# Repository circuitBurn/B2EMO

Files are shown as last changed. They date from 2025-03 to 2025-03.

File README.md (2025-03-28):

# B2EMO

### Build Log

#### March 26, 2025
This is still under development!

The PCB is undergoing a revision and will be released once it is built and tested.

I am adding a temporary wiring diagram and for anyone wanting to implement the automated inner ring control.

## Bill of Materials
[BOM](https://github.com/circuitBurn/B2EMO/blob/development/BOM.pdf)

## RF System
* [FrSky Archer Plus R12+](https://www.frsky-rc.com/product/archer-plus-r12/)
* [Horus X10S Express](https://www.frsky-rc.com/product/horus-x10s-express/)

## Arduino Libraries
* [Countdown](https://github.com/RobTillaart/CountDown)
* [DFPlayerMini_Fast](https://github.com/PowerBroker2/DFPlayerMini_Fast)
* [Bolderflight SBUS](https://github.com/bolderflight/sbus)

## Circuit Diagram
This is a temporary circuit diagram outlining the minimum circuit needed to get the ESP32 controlling the ring motors. This will be updated once the PCB is completed.

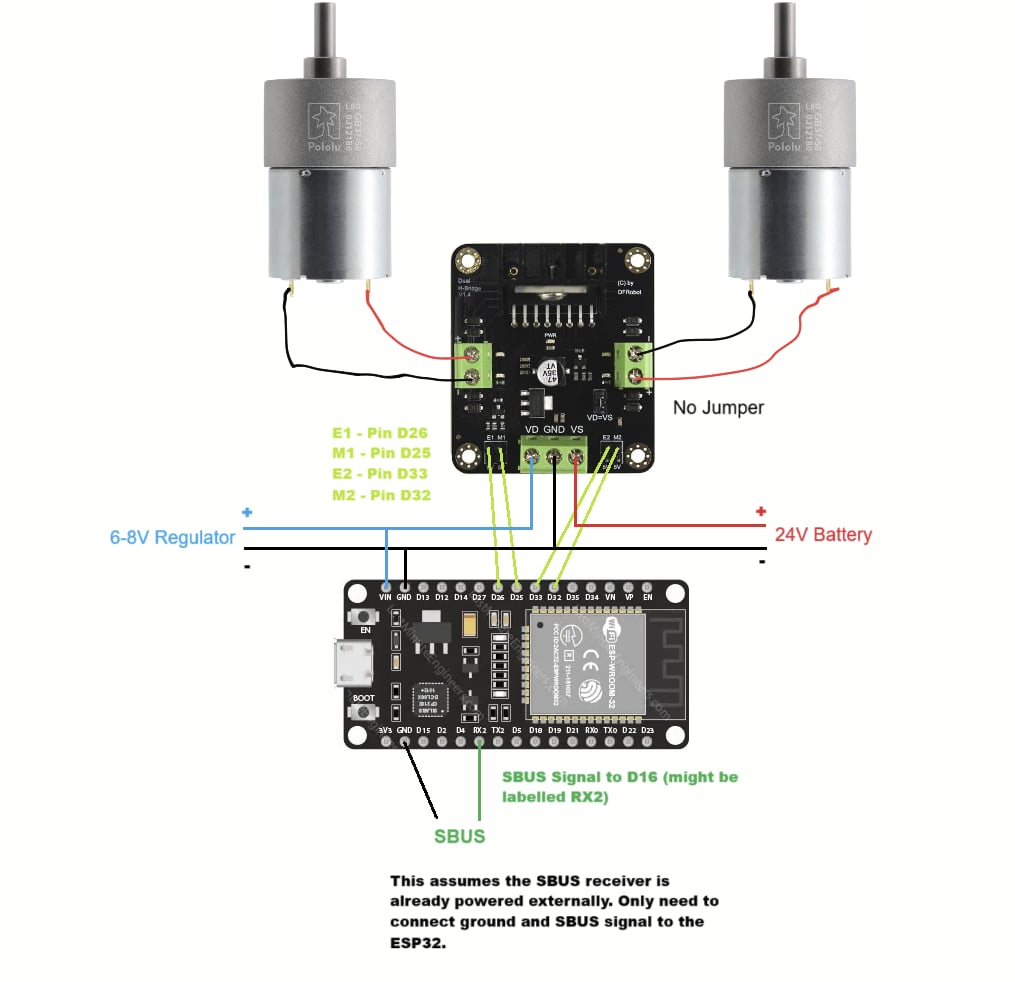
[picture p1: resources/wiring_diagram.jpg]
Wiring Diagram


## PCB
PCB is still in beta and is not the final design.

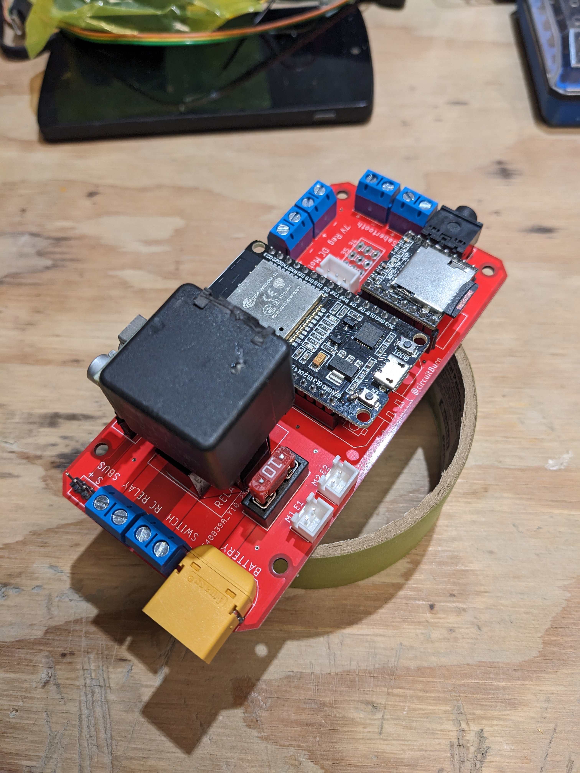
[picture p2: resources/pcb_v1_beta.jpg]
PCB


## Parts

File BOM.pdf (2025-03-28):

Part | Quantity | Part # | Store | URL | Description
5V, 3.2A Step-Down Voltage Regulator | 1 D36V28F5 | Pololu | https://www.pololu.com/product/3782 | Provides 5V to ESP32, DFPlayer,
Pololu 7.5V, 15A Step-Down Voltage Regulator | 1 D24V150F7 | Pololu | https://www.pololu.com/product/2883 | Provides power to RX, servos, motor controller logic
RC Relay | 1 RB-Pol-309 | Pololu | https://ca.robotshop.com/products/pololu-rc-switch-relay RC Relay to trigger main 24V relay
2A Dual Motor Controller | 1 DRI0002 | DFRobot | https://www.dfrobot.com/product-66.html | Drives 2 x 24V data ring motors
MP3 Player | 1 | 1121 DFRobot | https://www.dfrobot.com/product-1121.html | MP3 Player
1k ohm 1/4W resistor | 1 CF14JT1K00CT-ND | DigiKey | https://www.digikey.ca/en/products/detail/stackpole-electronics-inc/CF14JT1K00/1741314 1k Resistor for RX pin of DFPlayer
2pos 5mm pitch screw terminals | 4 ED2600-ND | DigiKey | https://www.digikey.ca/en/products/detail/on-shore-technology-inc/OSTTC020162/614549 Main power switch, RC relay, 2 x 24V outputs
Fuse holder | 1 36-3568-ND | DigiKey | https://www.digikey.ca/en/products/detail/keystone-electronics/3568/2137306 Main power fuse holder
Relay Socket | 1 HD-1003 | DigiKey | https://www.digikey.ca/en/products/detail/cit-relay-and-switch/hd-1003/12503026 Main relay socket
CONN JACK STEREO 3.5MM PCB R/A | 1 2092-STX-3120-3B-ND | DigiKey | https://www.digikey.ca/en/products/detail/kycon-inc/STX-3120-3B/9990113 Audio out from DFPlayer
24V 40A Relay | 1 | Amazon | https://www.amazon.ca/dp/B07P8614R4?ref=ppx_yo2ov_dt_b_fed_asin_title Main power relay
90 degree XT60 male connector | 1 | Amazon | https://www.amazon.ca/dp/B09XTN9N9S?ref=ppx_yo2ov_dt_b_fed_asin_title Battery connector
2pos JST Conncetor | 2 | Amazon | https://www.amazon.ca/Glarks-JST-XHP-Housing-Adapter-Connector/dp/B07CTH46S7/ref=sr_1_1_sspa JST Connectors
Header pins (male and female of various sizes) | N/A | Amazon | https://www.amazon.ca/Glarks-Connector-Assortment-Stackable-Breakaway/dp/B07CWSXY7P/ref=sr_1_1_sspa For SBUS in, ESP32, DFPlayer, 5V regulator
ESP32 | 1 | Amazon | https://www.amazon.ca/ELEGOO-ESP-WROOM-32-Development-Bluetooth-Microcontroller/dp/B0D8SXGL9C/ref=sr_1_1_sspa Any ESP32 Devkit with similar pinout will do

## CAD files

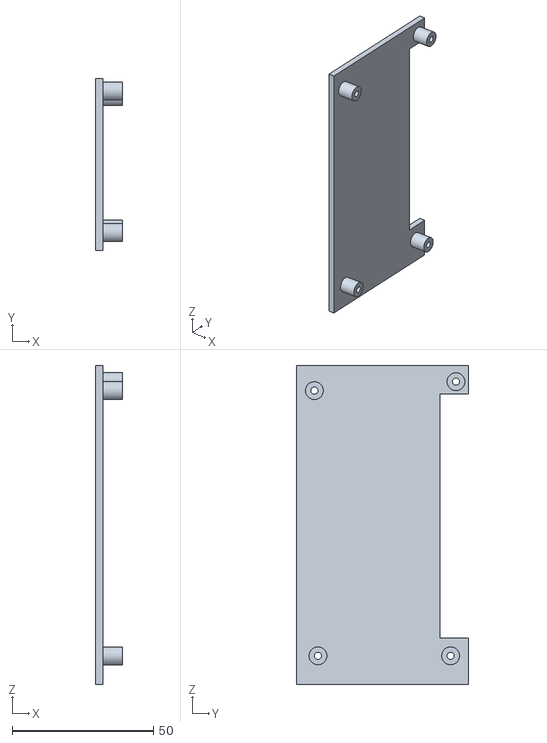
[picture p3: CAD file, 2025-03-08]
3d print files/pcb_mount.stl
9.52 x 61.0 x 113.0

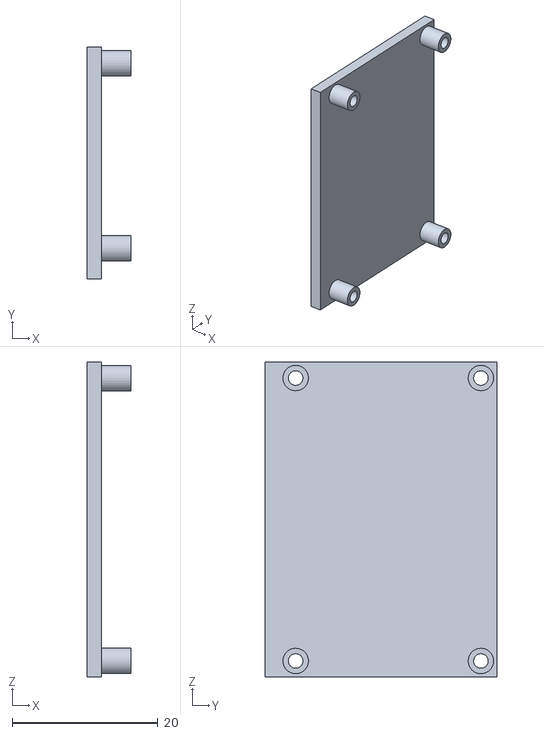
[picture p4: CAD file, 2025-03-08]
3d print files/pololu_D24V150Fx_regulator.stl
6.00 x 31.8 x 43.2

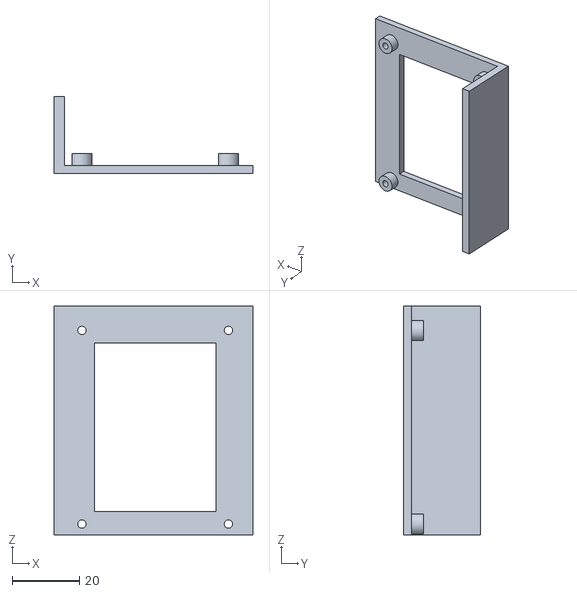
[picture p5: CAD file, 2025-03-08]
3d print files/amplifier.stl
59.0 x 23.0 x 68.0

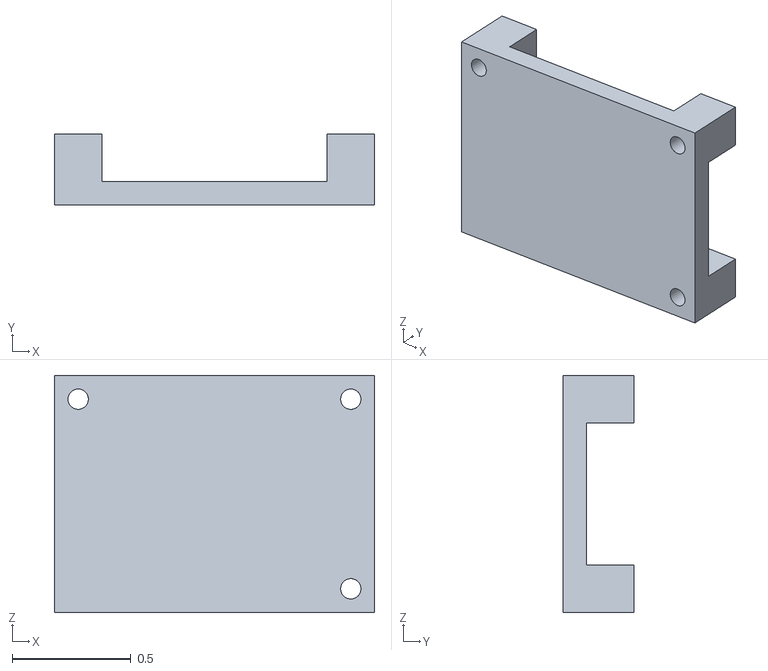
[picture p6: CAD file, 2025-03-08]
3d print files/pololu_rc_relay.stl
1.35 x 0.3 x 1.00

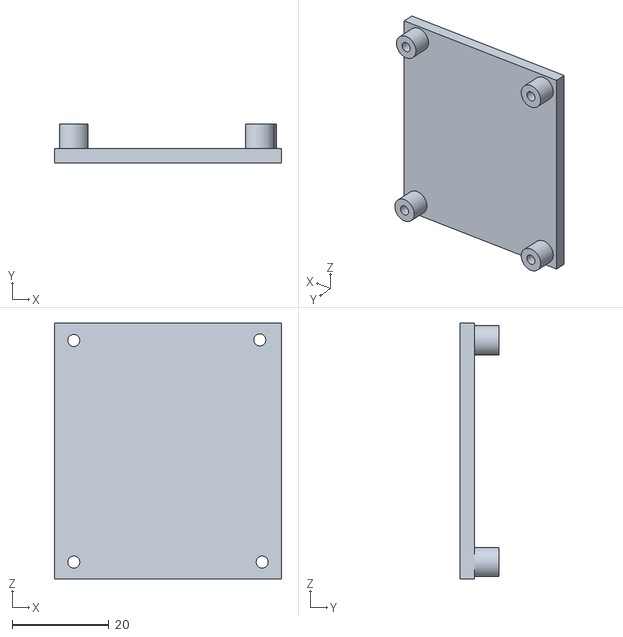
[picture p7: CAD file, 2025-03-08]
3d print files/dual_h_bridge_mount.stl
47.0 x 8.00 x 53.0

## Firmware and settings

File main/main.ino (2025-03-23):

#include <DFPlayerMini_Fast.h>
#include "sbus.h"
#include <SoftwareSerial.h>
#include "CountDown.h"
#include "DataRingState.h"

// SBUS RC values
constexpr int RC_HIGH = 1811;
constexpr int RC_MID = 992;
constexpr int RC_LOW = 172;

// Channels (Offset by 1 from transmitter: Channel 1 on TX is 0 here)
constexpr int CH_DATA_RINGS = 14;
constexpr int CH_MP3_TRIG = 15;

// SBUS communication pins
constexpr int SBUS_RX = 16;
constexpr int SBUS_TX = 17;

// DFPlayer module pins
constexpr int MP3_RX = 18;
constexpr int MP3_TX = 19;
constexpr int MP3_BUSY = 23;

// Data ring motor control pins
constexpr int M1 = 25;
constexpr int E1 = 26;
constexpr int M2 = 32;
constexpr int E2 = 33;
constexpr int DATA_RING_SPEED = 110; // 0 - 255

// Data ring timers used to randomize spin/stop
CountDown e1Timer;
CountDown e2Timer;

// DFRobot motor controller control values
bool e1Direction = LOW;
int e1Speed = 0;
bool e2Direction = LOW;
int e2Speed = 0;

// Randomized spin and delay values
int spinLow = 0;
int spinHigh = 0;
int delayLow = 0;
int delayHigh = 0;

// FrSky SBUS
bfs::SbusRx sbus_rx(&Serial1, SBUS_RX, SBUS_TX, true);
bfs::SbusData data;

// DFPlayer Mini
SoftwareSerial mySerial(MP3_RX, MP3_TX);
DFPlayerMini_Fast dfPlayer;

// Sound trigger button debounce
const int debounceDelay = 50;
int lastStableValue = -1;
unsigned long lastDebounceTime = 0;

void setup()
{
  pinMode(M1, OUTPUT);
  pinMode(E1, OUTPUT);
  pinMode(M2, OUTPUT);
  pinMode(E2, OUTPUT);

  mySerial.begin(9600);
  dfPlayer.begin(mySerial, true);
  dfPlayer.volume(8);

  sbus_rx.Begin();
}

void loop()
{
  if (sbus_rx.Read())
  {
    data = sbus_rx.data();
    playTriggeredSound();
    controlDataRingMotors();
  }
}

void controlDataRingMotors()
{
  // Read the data ring mode selection switch
  DataRingState state = getDataRingSwitchState();
  switch (state)
  {
    case DataRingState::FAST:
      {
        // Set shorter spin and delay times (ms)
        spinLow = 100;
        spinHigh = 400;
        delayLow = 500;
        delayHigh = 500;
        break;
      }
    case DataRingState::SLOW:
      {
        // Set longer spin and delay times (ms)
        spinLow = 150;
        spinHigh = 750;
        delayLow = 800;
        delayHigh = 2500;
        break;
      }
    case DataRingState::IDLE:
      {
        // Stop all timers and turn off the motors
        // Returns immediately since we don't need to check anything else
        e1Speed = 0;
        e2Speed = 0;
        e1Timer.stop();
        e2Timer.stop();
        updateMotor(M1, E1, e1Direction, e1Speed);
        updateMotor(M2, E2, e2Direction, e2Speed);
        return;
      }
  }

  // Start upper ring
  if (e1Timer.isStopped() && e1Speed == 0)
  {
    // Set a randomized spin time
    e1Timer.start(random(spinLow, spinHigh));

    // Randomize direction
    e1Direction = random(0, 2);

    // TODO: randomize speed
    e1Speed = DATA_RING_SPEED;
  }

  // Start lower ring
  if (e2Timer.isStopped() && e2Speed == 0)
  {
    // Set a randomized spin time
    e2Timer.start(random(spinLow, spinHigh));

    // Randomize direction
    e2Direction = random(0, 2);

    // TODO: randomize speed
    e2Speed = DATA_RING_SPEED;
  }

  // Stop upper ring
  if (e1Timer.isStopped() && e1Speed == DATA_RING_SPEED)
  {
    e1Speed = 0;

    // Set a randomized delay before starting again
    e1Timer.start(random(delayLow, delayHigh));
  }

  // Stop lower ring
  if (e2Timer.isStopped() && e2Speed == DATA_RING_SPEED)
  {
    e2Speed = 0;

    // Set a randomized delay before starting again
    e2Timer.start(random(delayLow, delayHigh));
  }

  updateMotor(M1, E1, e1Direction, e1Speed);
  updateMotor(M2, E2, e2Direction, e2Speed);
}

/**
   Returns the state corresponding to the data ring mode selector switch on the transmitter
*/
DataRingState getDataRingSwitchState()
{
  if (data.ch[CH_DATA_RINGS] == RC_LOW)
  {
    return DataRingState::FAST;
  }
  else if (data.ch[CH_DATA_RINGS] == RC_MID)
  {
    return DataRingState::SLOW;
  }

  return DataRingState::IDLE;
}

/**
   Communicate with a single motor on the motor controller
*/
void updateMotor(int motor, int enable, bool direction, int speed)
{
  digitalWrite(motor, direction);
  analogWrite(enable, speed);
}

/**
   Read the sound button index from 1 to 10
*/
int getSoundIndex(int triggerValue)
{
  static int lastValue = -1;
  static unsigned long lastTime = 0;
  unsigned long currentTime = millis();

  // If the value is unstable, reset debounce timer
  if (triggerValue != lastValue)
  {
    lastTime = currentTime;
  }

  // If stable for debounceDelay, accept new value
  if ((currentTime - lastTime) > debounceDelay)
  {
    lastStableValue = triggerValue;
  }

  lastValue = triggerValue;

  // Process only the stable value
  if (lastStableValue < 172 || lastStableValue > 1680)
  {
    return -1;
  }
  return 10 - (lastStableValue - 172) / 180;
}

/**
 * Play the triggered sound immediately
 */
void playTriggeredSound()
{
  int soundIndex = getSoundIndex(data.ch[CH_MP3_TRIG]);
  if (soundIndex > 0)
  {
    dfPlayer.play(soundIndex);
  }
}

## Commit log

2025-01-18 Adding first draft of 3d printable PCB mounts
    [pcb_mount.stl, pololu_D24V150Fx_regulator.stl, pololu_rc_relay.stl]
2025-01-18 Initial commit of Arduino sketches
2025-03-08 Updates to arduino
2025-03-08 Adding and modifying STL files
    [amplifier.stl, dual_h_bridge_mount.stl, pcb_mount.stl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]
2025-03-18 Including Arduino libraries in README
2025-03-23 Reversing motor control pins
    [main.ino]
2025-03-26 Adding temporary wiring diagram
